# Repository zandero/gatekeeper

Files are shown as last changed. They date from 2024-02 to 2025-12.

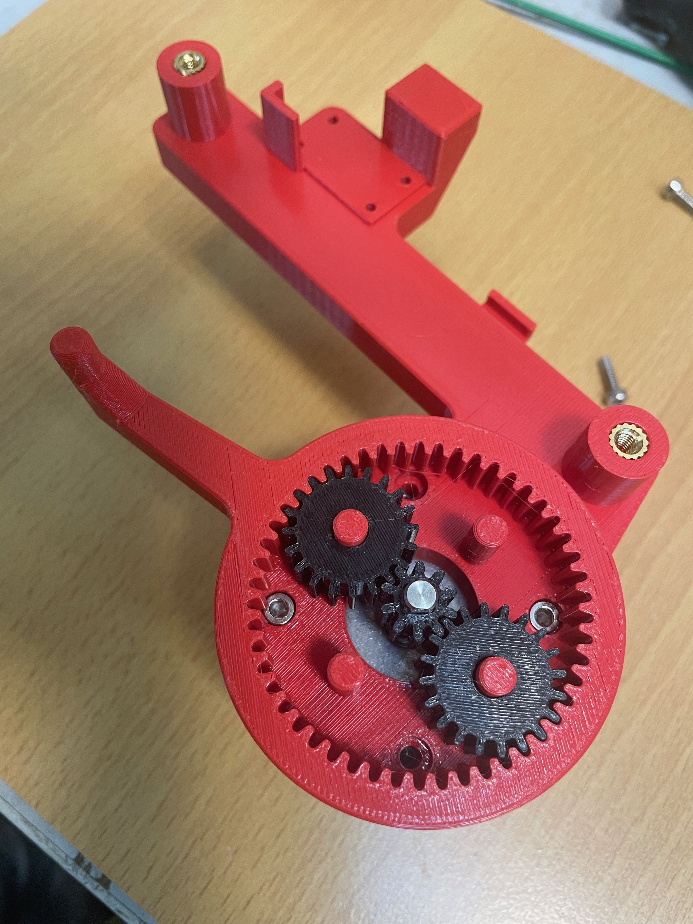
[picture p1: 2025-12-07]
3D_print/DX100G_blast_gate_100mm_V2/MotorSunGearAssembly.jpeg

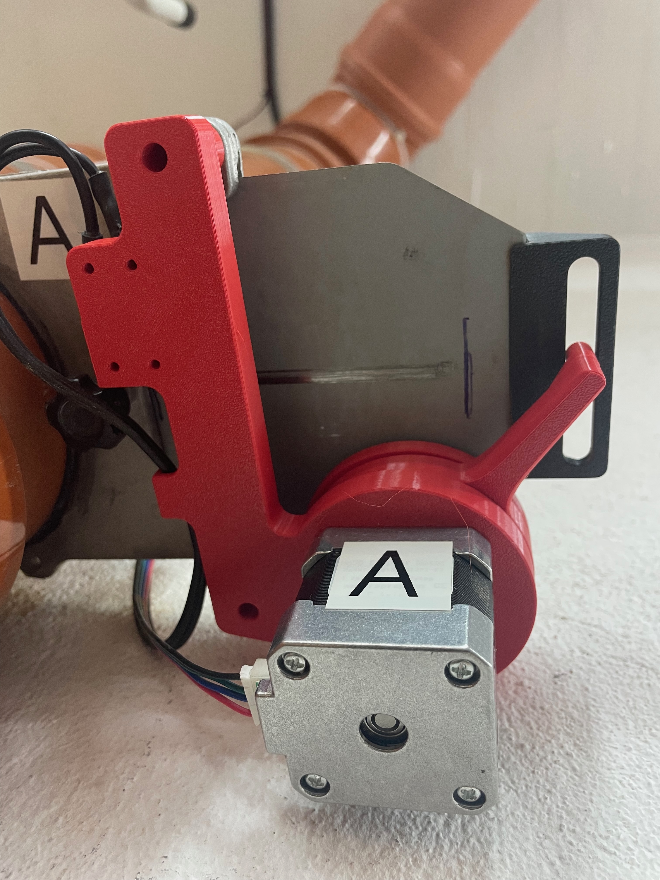
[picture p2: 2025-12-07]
3D_print/DX100G_blast_gate_100mm_V2/GateAssembled_BottomView.jpeg

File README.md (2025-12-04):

# Arduino-Controlled Automated Dust Blast Gates for Woodworkers

This project aim is to assist fellow woodworkers in creating their own cost-effective automated blast gates.

> **NOTE: This is quite an involved build.**  
> Apart from the hardware, you will also need:
> - to 3D print some parts (or design your own)   
> - Solder and connect all parts together
> - Measure current/voltage of the stepper motor drivers to trim them  
> - Modify the main.cpp code to fit your setup (see below)

# How does it work / operation
The Arduino board 
- Monitors the operating status of machines through a current measuring sensor.
- Activates/deactivates the relevant blast gate(s) based on the specific machine in use - i.e. signals the stepper motors to open/close a gate.
- Maintain the gate(s) in the opened or closed position until another machine is powered on.

## Capabilities

- Control up to 5 individual blast gates
- Monitor 5+ machines (limited by the number of analog inputs)

## Required hardware

> Excluded the dust collection system and manual gates

### Control centre:

- Arduino Mega 2560
- Ramps 1.4 shield (or later)
- DC 12V 10A power supply
- Enclosure for Arduino and power supply
- Master on/off mains switch (220V)

#### Voltage regulation (for AC sensor)

- 1 x Burden resistor 18 Ohms if supply voltage is 3.3V, or 33 Ohms if supply voltage is 5V
- 2 x 10k Ohm resistors (or any equal value resistor pair up to 470k Ohm)
- 1 x 10uF capacitor

### Dust gate (per gate):

- Nema 17 stepper motor
- DRV8825 (highly recommended) alternatively A4988 (not recommended might run very hot)
- 3.5mm DC audio plug (male/female) to connect blast gate switches to Arduino
- Micro Limit Switch

### Machine monitoring (per machine):

- SCT-013-000 Non-invasive AC Sensor with Split Core Transformer 100A
- 3.5mm DC audio plug (male/female) to extend reach of sensor

### Additional small hardware
- Stepper motor control wires
- Double core wire (to connect sensors and gate switches with Arduino) (shielded if possible)
- M3x6 thread inserts for 3D printing
- M4x6 thread inserts for 3D printing
- M3 and M4 screws for mounting
- self-tapping screws (various sizes)
- zip ties (a lot in various sizes)
- Soldering wire / heat shrinks ...

## Estimated cost (minimal)

> Costs were estimated on Feb. 2024

| Item | Approximate price |
|---|---|
| Arduino Mega | 38 EUR |
| Ramps 1.4 | 9 EUR | 
| DRV8825 Step Motor Driver Module | 15 EUR pack of 5 (3 EUR per driver) |
| voltage regulation components | 5 EUR |
| DC 12V 10A power supply | 20 EUR |
| | |
| Nema 17 stepper motor (1.7A or more) | 35 EUR pack of 5 (7 EUR per motor) |
| Micro Limit Switch | 16 EUR pack of 10 (1.6 EUR per switch) |
| Stepper motor cables (2m) | 10 EUR pack of 6 (1.5+ EUR per cable) |
| | |
| 3.5 audio plugs | 9 EUR pack of 10 (1 EUR per plug) |
| SCT-013-000 AC sensor | 10 EUR |
| | |
| **Total minimal cost**: | 71 EUR + (14 EUR per gate) + (11 EUR per machine) |

> **Example**  
> For a setup with 4 gates and 3 machines the total minimal cost would be around **160EUR**
>
> Estimate additional 10-20% for material like wires, heat shrinks, screws, etc.
> 
> Costs can vary vastly depending on where you source your materials (this is just a ballpark estimation) 

## Limitations

The main limitation of this setup is the distance between the blast gate and the control centre (i.e. Arduino board)

I have been only able to find stepper motor cables that are 2m long - limiting the max distance between gates to 4m (13
feet). One can probably make your own stepper motor cables that are longer - not sure what the maximum length could be.

The machine monitoring cables run im my case up to 10m long without any issues.

# Getting started (the software)

Install all needed software:
- [Download and install git](https://git-scm.com/downloads) 
- checkout project from GitHub  
  > git clone https://github.com/zandero/gatekeeper.git
- install [Visual Studio Code](https://code.visualstudio.com/download)
- add [PlatformIO](https://platformio.org/install/ide?install=vscode) plugin to `Visual Studio Code`

## Build the project

## Setup main.cpp 
In order to make things work correctly you will need to modify the main logic in [main.cpp](./GateKeeper/src/main.cpp) according to your setup

- define energy monitoring pin(s) (`JOINTER_PIN`, `CIRCULAR_SAW_PIN`, ...)
- define the voltage/amperage limit when gate should move (`MOTOR_A_STEP_PIN`, `MOTOR_A_DIR_PIN`, `MOTOR_A_ENABLE_PIN`, ...) 
- define gate close switch and motor pin(s) (`SWITCH_GATE_A`, ...), 

### Alter helper functions according to your setup

# The logic

## setup()

In the `setup()` step the gates and energy monitoring is initialized.   
The code "waits" until all:
- energy monitors report a value below the given threshold (i.e. all machine must be turned off)
- and all gates report that they are closed (all gete close switches are engaged)

## loop()

Once the initial state (all gates closed, no machine running) is detected the code "monitors" each machine consumption.  
Once a spike in consumption is detected (i.e. a machine is running) the appropriate gates are opened/closed.

> NOTE: once gates are in movement energy monitoring is suspended. 
> This is due to the very slow operation of consumption check. 
> Only when all gates finish their move the energy monitoring is resumed.

# The hardware

## #1 Current/voltage detection
In order to accurately detect if a machine is running the output signal from the CT sensor needs to be conditioned, so it 
meets the input requirements of the Arduino analog inputs, i.e. a positive voltage between 0V and the ADC reference voltage.

[See this guide](https://docs.openenergymonitor.org/electricity-monitoring/ct-sensors/how-to-build-an-arduino-energy-monitor-measuring-current-only.html)

Assuming only one machine will be running at once / multiple sensors can be connected to the same circuit.   
If you are planing to run multiple machines simultaneously you will need to provide on circuit for each sensor.

## #2 Defining motor rotation and travel
### Stepper motor rotation

### Tuning the stepper drivers
If the stepper motors can't push the gate to close/open (they are skipping steps) we might need to boost the stepper driver voltage.
This will happen if the gates are mounted in such way that the motors must also resist the force of gravity i.e. gates are mounted vertically.

To find out the maximum allowed voltage you need to consired the rated current of your stepper motor.  
See the following guides:
- [general on how to do this](https://www.youtube.com/watch?v=BV-ouxhZamI)  
- [guide for DRV8825](https://lastminuteengineers.com/drv8825-stepper-motor-driver-arduino-tutorial/)

> Example: for a **1.7A** NEMA motor you will shoot for **0.85V** 

## #3 Defining machine consumption threshold 

## #4 Build a simple one gate one machine prototype
Before venturing on a full build it is recommended to check if every component is working as expected by building a simple prototype.

## #5 Putting it all together 

Putting it all together

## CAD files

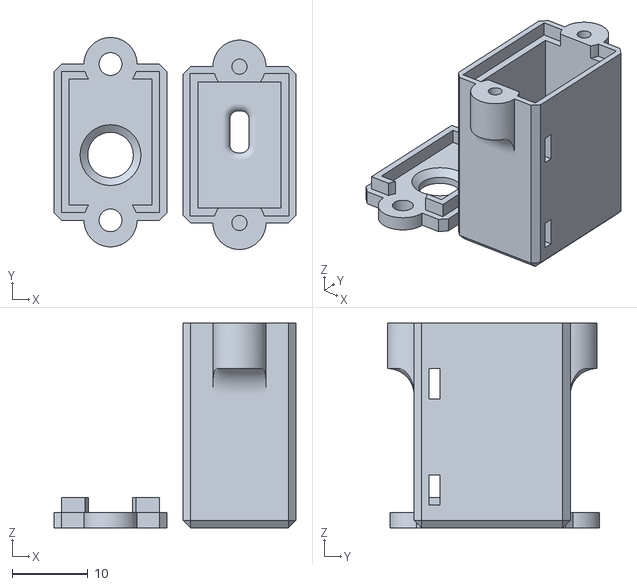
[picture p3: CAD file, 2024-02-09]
3D_print/CurrentSensor/SensorConnector.stl
31.9 x 27.9 x 27.0

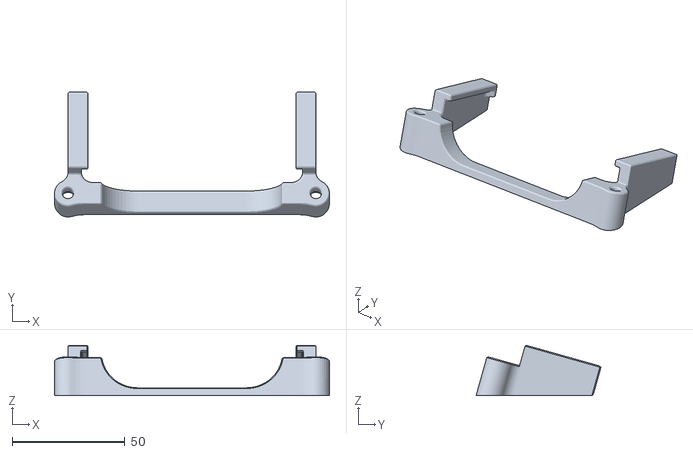
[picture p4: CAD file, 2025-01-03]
3D_print/DX100G_blast_gate_100mm/BlastGateGuide.stl
122.0 x 55.4 x 22.3

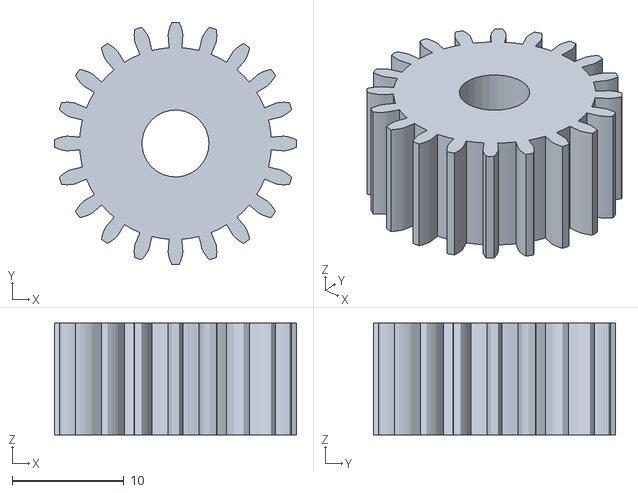
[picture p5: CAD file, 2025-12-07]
3D_print/DX100G_blast_gate_100mm_V2/PlanetaryGear.stl
21.7 x 21.7 x 10.0

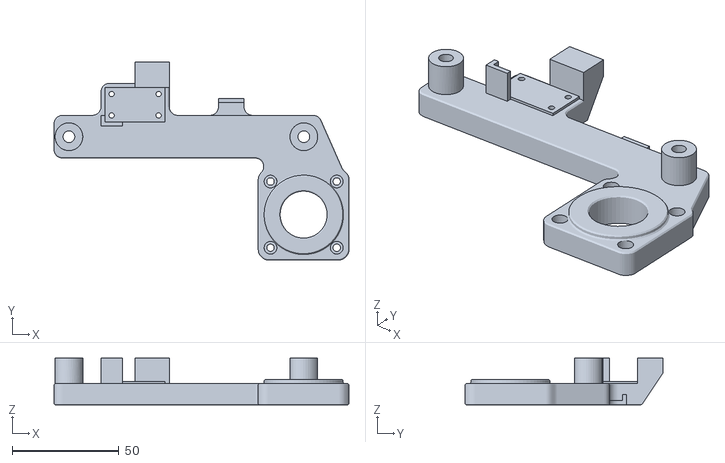
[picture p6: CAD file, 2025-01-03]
3D_print/DX100G_blast_gate_100mm/MotorGateMount.stl
138.2 x 92.7 x 22.0

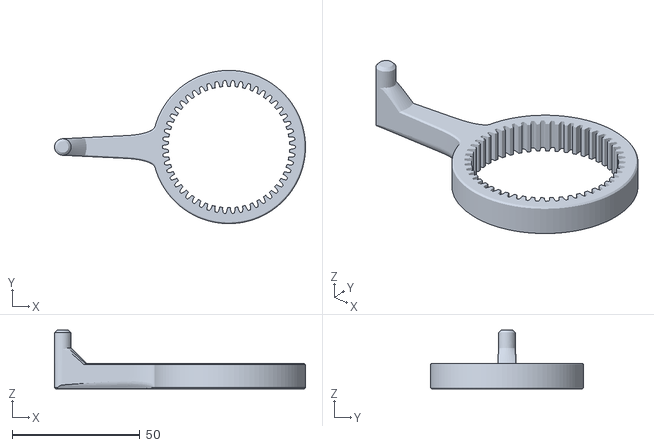
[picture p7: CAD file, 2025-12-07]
3D_print/DX100G_blast_gate_100mm_V2/LeverSpurGear.stl
98.2 x 60.0 x 23.0

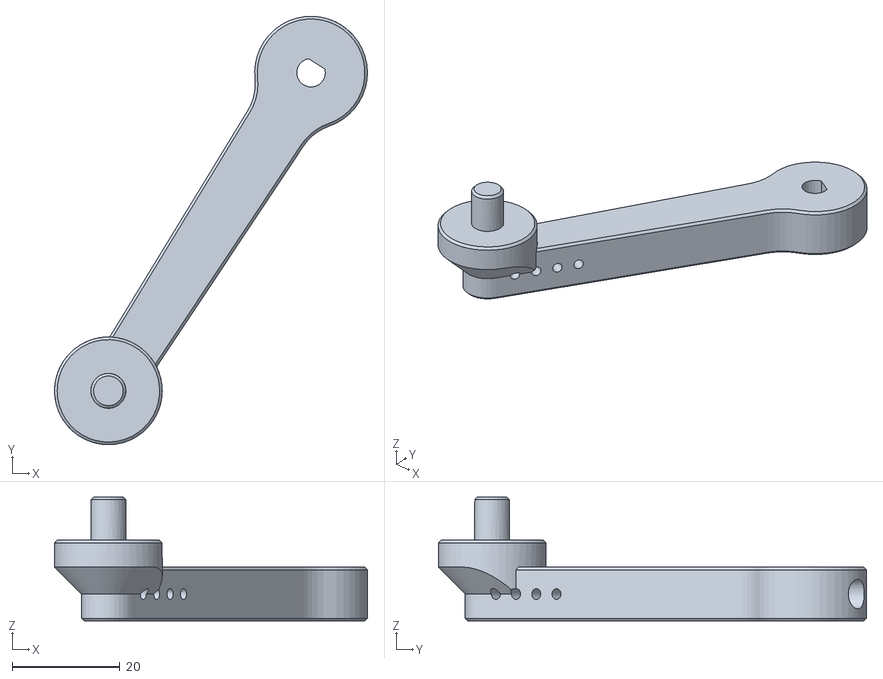
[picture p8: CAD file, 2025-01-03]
3D_print/DX100G_blast_gate_100mm/Lever.stl
58.1 x 79.5 x 23.0

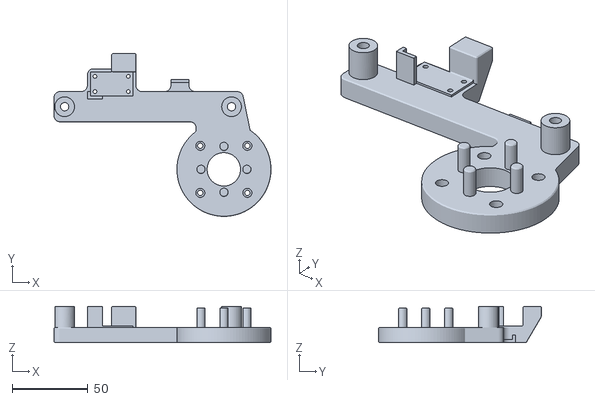
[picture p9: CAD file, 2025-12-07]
3D_print/DX100G_blast_gate_100mm_V2/MotorMount.stl
143.0 x 107.2 x 24.0

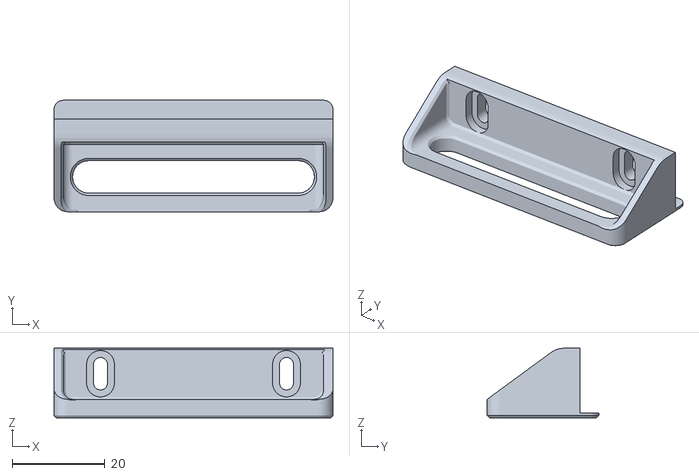
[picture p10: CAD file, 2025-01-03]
3D_print/DX100G_blast_gate_100mm/BlastGateTounge.stl
60.0 x 24.0 x 15.0

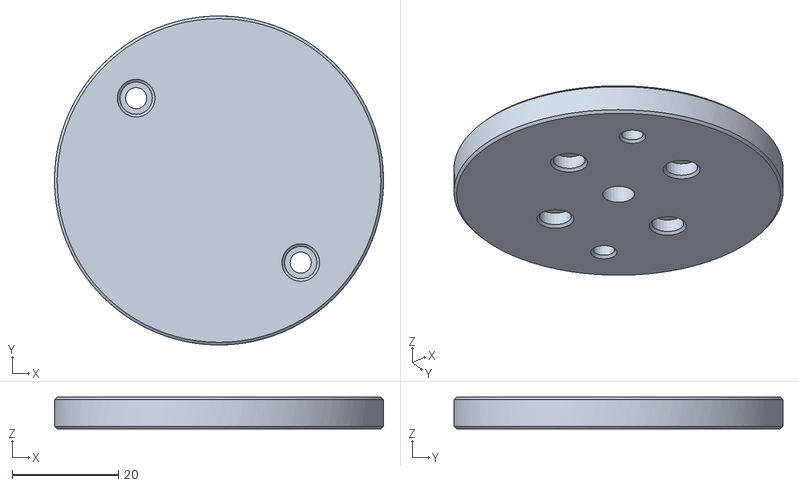
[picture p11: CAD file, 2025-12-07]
3D_print/DX100G_blast_gate_100mm_V2/MotorGearCover.stl
62.0 x 62.0 x 6.00

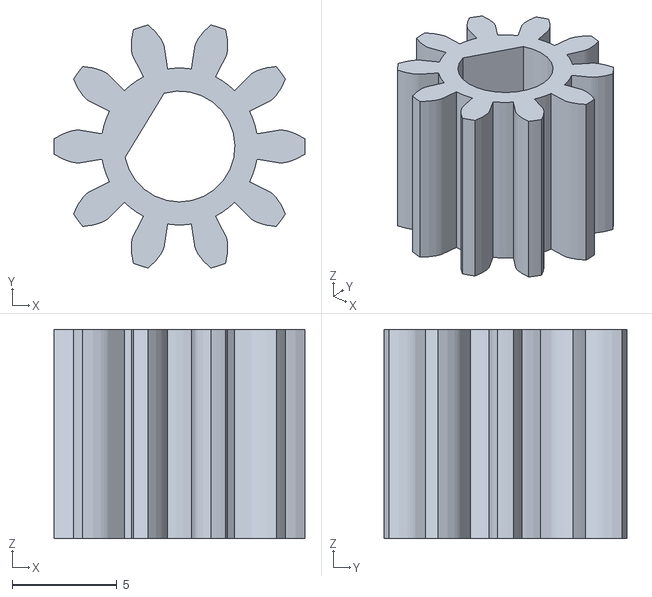
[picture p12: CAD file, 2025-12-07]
3D_print/DX100G_blast_gate_100mm_V2/SunGear.stl
12.0 x 11.6 x 10.0

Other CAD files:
3D_print/DX100G_blast_gate_100mm_V2/GateTounge.stl

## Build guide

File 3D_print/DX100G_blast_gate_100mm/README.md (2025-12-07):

# Blast gate motor mounting hardware

The 3D printed parts are based on the Record Power DX100G Blast Gate 100mm

https://www.recordpower.co.uk/product/100mm-dust-extraction-blast-gate

# Check latest Version V2

Version V2 improves on:
- the sun gear arrengment improves closing/opening tourque (opening and closing)
- the gate stays in position even when motors are not powered

## Important
- make sure you align the gears correctly / when misaligned some tooth might skip
- three planetary gears are possible but then the screws for the cover are blocked therefore two planetary gears
- greasing the gears is not necessary but will not hurt

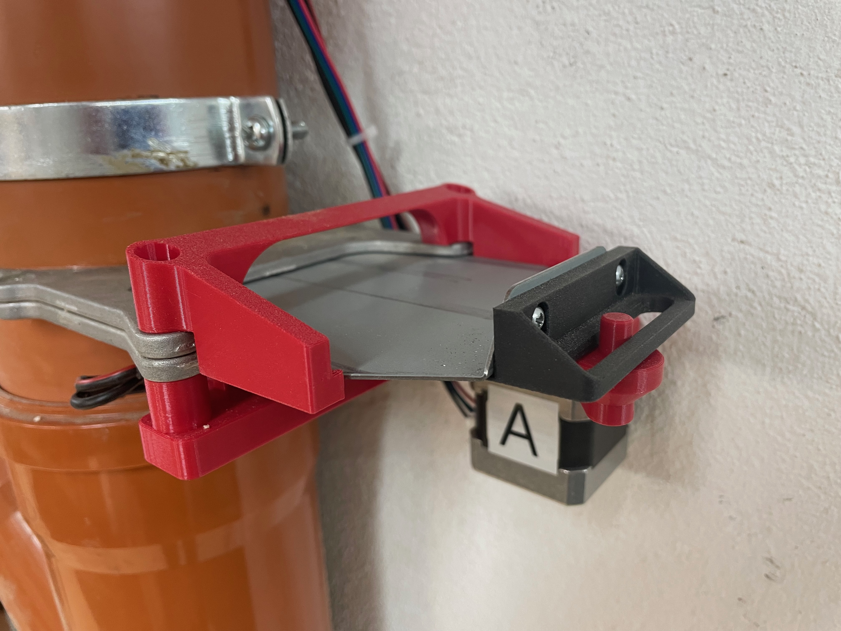
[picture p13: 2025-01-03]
3D_print/DX100G_blast_gate_100mm/BlastGateAssembled_Top.jpeg

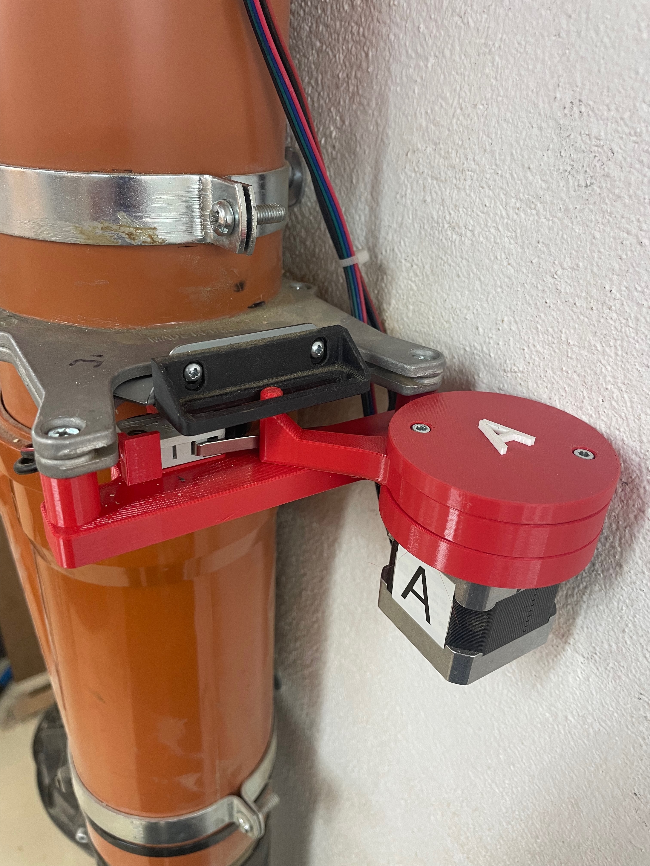
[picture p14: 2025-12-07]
3D_print/DX100G_blast_gate_100mm_V2/GateAssembled.jpeg

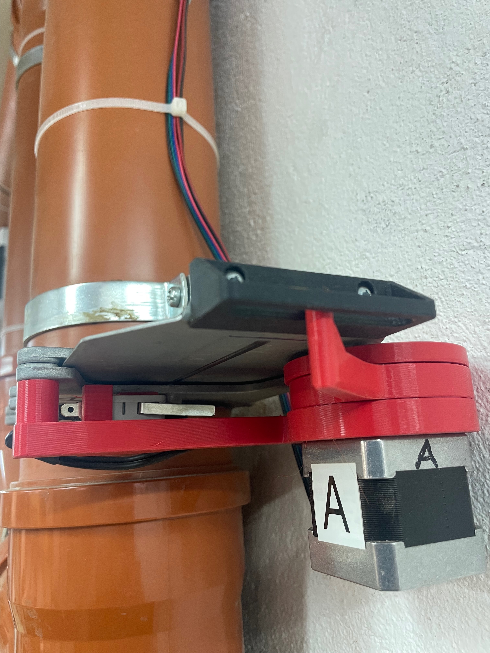
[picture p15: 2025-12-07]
3D_print/DX100G_blast_gate_100mm_V2/GateAssembled_SideView.jpeg

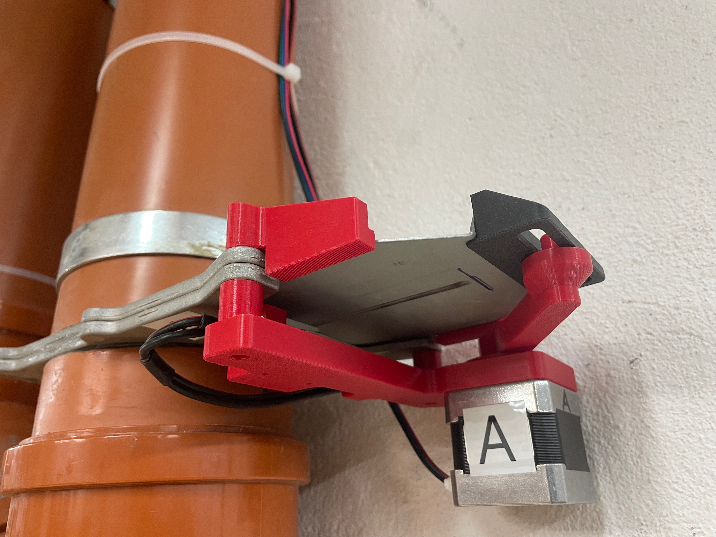
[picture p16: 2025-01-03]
3D_print/DX100G_blast_gate_100mm/BlastGateAssembled_Bottom.jpeg

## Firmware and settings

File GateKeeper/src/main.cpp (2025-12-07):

#include <Arduino.h>
#include "BlastGate.h"
#include "MachineMonitor.h"
#include "BlinkLight.h"

// Added for easier debug on/off of serial messages
// (set DEBUG=false) once everything is running as expected (but can be left on DEBUG=true - does not affect the functionality)
#define DEBUG true
#ifdef DEBUG == true
  #define debug(x) Serial.print(x)
  #define debugln(x) Serial.println(x)
#else
  #define debug(x)
  #define debugln(x)
#endif

// Machine energy monitors
#define JOINTER_PIN 3           // A3 (red)
#define CIRCULAR_SAW_PIN 4      // A4 (yellow)
#define BAND_SAW_PIN 5          // A5 (blue)

// Gate switches
#define SWITCH_GATE_A 14   // D14 green
#define SWITCH_GATE_B 15   // D15 white
#define SWITCH_GATE_C 18   // D18 purple
#define SWITCH_GATE_D 19   // D19 black

// Gate motors
#define MOTOR_A_STEP_PIN 54     // X - axis
#define MOTOR_A_DIR_PIN 55
#define MOTOR_A_ENABLE_PIN 38

#define MOTOR_B_STEP_PIN 60     // Y - axis
#define MOTOR_B_DIR_PIN 61
#define MOTOR_B_ENABLE_PIN 56

#define MOTOR_C_STEP_PIN 46     // Z - axis
#define MOTOR_C_DIR_PIN 48
#define MOTOR_C_ENABLE_PIN 62

#define MOTOR_D_STEP_PIN 26     // E0 - axis
#define MOTOR_D_DIR_PIN 28
#define MOTOR_D_ENABLE_PIN 24

// motor speed and max open position
#define MAX_MOTOR_SPEED 700L
#define OPEN_ROTATION 7000L     // (recommended for DX100G Blast Gate 100mm with DRV8825 stepper driver)

// if you are using some other driver and stepper motors this value might be different

// Max amperage level for each machine
#define CIRCULAR_SAW_RUNNING 12
#define JOINTER_RUNNING 14
#define BAND_SAW_RUNNING 3.5

// Led lights PINs by gate
#define LED_PIN_A 17
#define LED_PIN_B 23
#define LED_PIN_C 25
#define LED_PIN_D 27
#define LED_BLINK_MS 75

// Associate motor and gate switches
BlastGate gateA(MOTOR_A_ENABLE_PIN, MOTOR_A_STEP_PIN, MOTOR_A_DIR_PIN, OPEN_ROTATION, SWITCH_GATE_A, true);
BlastGate gateB(MOTOR_B_ENABLE_PIN, MOTOR_B_STEP_PIN, MOTOR_B_DIR_PIN, OPEN_ROTATION, SWITCH_GATE_B, true);
BlastGate gateC(MOTOR_C_ENABLE_PIN, MOTOR_C_STEP_PIN, MOTOR_C_DIR_PIN, OPEN_ROTATION, SWITCH_GATE_C, true);
BlastGate gateD(MOTOR_D_ENABLE_PIN, MOTOR_D_STEP_PIN, MOTOR_D_DIR_PIN, OPEN_ROTATION, SWITCH_GATE_D, true);

// Set max amperage levels for each machine
MachineMonitor jointer(JOINTER_PIN, JOINTER_RUNNING);
MachineMonitor bandSaw(BAND_SAW_PIN, BAND_SAW_RUNNING);
MachineMonitor circularSaw(CIRCULAR_SAW_PIN, CIRCULAR_SAW_RUNNING);

// Optional gate light indicators 
// Closed = Led on
// Moving = Led blinking
// Open   = Led off
BlinkLight gateLightA(LED_PIN_A, LED_BLINK_MS);
BlinkLight gateLightB(LED_PIN_B, LED_BLINK_MS);
BlinkLight gateLightC(LED_PIN_C, LED_BLINK_MS);
BlinkLight gateLightD(LED_PIN_D, LED_BLINK_MS);


/** HELPER METHODS / alter according to your setup **/
/** Jointer line gates are OPEN, **/
bool jointerGatesOpen() {
  return gateA.isClosed() && 
         gateB.isOpen() && 
         gateC.isClosed() && 
         gateD.isOpen();
}

bool bandSawGatesOpen() {
  return gateA.isClosed() && 
         gateB.isOpen() && 
         gateC.isOpen() && 
         gateD.isClosed();
}

bool circularSawGatesOpen() {
  return gateA.isOpen() && 
         gateB.isClosed();
}

/** All gates are closed (needed on startup to)  **/
bool allGatesClosed() {
  return gateA.isClosed() && 
         gateB.isClosed() &&
         gateC.isClosed() &&
         gateD.isClosed();
}

/** Gate are not moving (each gate is either fully open or closed) **/
bool gatesAreNotMoving() {
  return !gateA.isMoving() && 
         !gateB.isMoving() && 
         !gateC.isMoving() && 
         !gateD.isMoving();
}

/** add here all MachineMonitor listeners **/
void sampleConsumption() {
  jointer.sample();
  bandSaw.sample();
  circularSaw.sample();
}

/** no machine is running (cunsumption is 'zero') **/
bool noMachineRunning() {
  return !jointer.isRunning() && 
         !circularSaw.isRunning() && 
         !bandSaw.isRunning();
}

void updateLights() {

  if (gateA.isClosed()) {
    gateLightA.on();
  }
  else if (gateA.isMoving()) {
    gateLightA.blink();
  }
  else {
    gateLightA.off();
  }

  //
  if (gateB.isClosed()) {
    gateLightB.on();
  }
  else if (gateB.isMoving()) {
    gateLightB.blink();
  }
  else {
    gateLightB.off();
  }

  //
  if (gateC.isClosed()) {
    gateLightC.on();
  }
  else if (gateC.isMoving()) {
    gateLightC.blink();
  }
  else {
    gateLightC.off();
  }

  //
  if (gateD.isClosed()) {
    gateLightD.on();
  }
  else if (gateD.isMoving()) {
    gateLightD.blink();
  }
  else {
    gateLightD.off();
  }

  gateLightA.update();
  gateLightB.update();
  gateLightC.update();
  gateLightD.update();
}


void setup() {

  if (DEBUG) {
    Serial.begin(9600);
    debugln("Starting up GateKeeper ... ");
  }

  // Wait until measurements get down low levels (no machine should be running)
  sampleConsumption();

  // close all gates (initialize to 0)
  while (!allGatesClosed() || !noMachineRunning()) {

    updateLights();

    if (!allGatesClosed()) {
      
      gateA.close();
      gateB.close(); 
      gateC.close();
      gateD.close();
      
      if (allGatesClosed()) {
        debugln("Gates initialized - all gates are closed");                  
      }
    }

    if (!noMachineRunning()) {      
      sampleConsumption();
      if (noMachineRunning()) {
        debugln("Energy monitoring initialized");
      }
    }
  }

  debugln("Initialization finished");
}


void loop() {

  updateLights();

  // measure current only when gates are not in movement
  // otherwise the gates will move very slow as measuring takes a lot of time
  if (gatesAreNotMoving()) {
  
    sampleConsumption();

    /* This part is only for logging and debugging purposes */
    if (jointer.isRunning() && !jointerGatesOpen()) {
      debugln("Jointer running - trigger open B / D, close A / C");
    }

    if (circularSaw.isRunning() && !circularSawGatesOpen()) {
      debugln("Circular saw running - trigger open A, close B");
    }

    if (bandSaw.isRunning() && !bandSawGatesOpen()) {
      debugln("Band saw running - trigger open B / C, close A / D");
    }
  }

  // The logic - set position of each gate if a machine is running
  // NOTE: It is assumed that only one machine is running!
  if (circularSaw.isRunning()) {
    gateA.open();
    gateB.close();
  }
  
  if (jointer.isRunning()) {
    gateA.close();
    gateB.open();
    gateC.close();
    gateD.open();
  }
  
  if (bandSaw.isRunning()) {
    gateA.close();
    gateB.open();
    gateC.open();
    gateD.close();
  }
}

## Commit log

2024-02-09 Added arduino control scripts
2024-02-09 Added 3D printing step/stl files
    [BlastGateTounge.step, BlastGateTounge.stl, Lever.step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]
2024-02-12 Moved project to VSCode / PlatformIO
    [BlastGateTounge.step, BlastGateTounge.stl, Lever.step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]
2024-02-14 Removed old arduino skript
2025-01-03 Improved blast gate motor mount and lever design
    [BlastGateGuide.stl, BlastGateTounge.step, BlastGateTounge.stl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]
2025-01-03 Removed unecessary duplicate file
    [SensorConnector.step]
2025-01-03 Newest version of blast gate designs added
    [BlastGateGuide.stl, GateGuide.step, Lever.stl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]
2025-12-04 Added option to invert motor spin via flag
    [main.cpp]
2025-12-07 Fixing inverse motor move logic
    [main.cpp]
2025-12-07 Added 3D models for version V2 of gate
    [GateTounge.stl, LeverSpurGear.stl, MotorGearCover.stl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]
